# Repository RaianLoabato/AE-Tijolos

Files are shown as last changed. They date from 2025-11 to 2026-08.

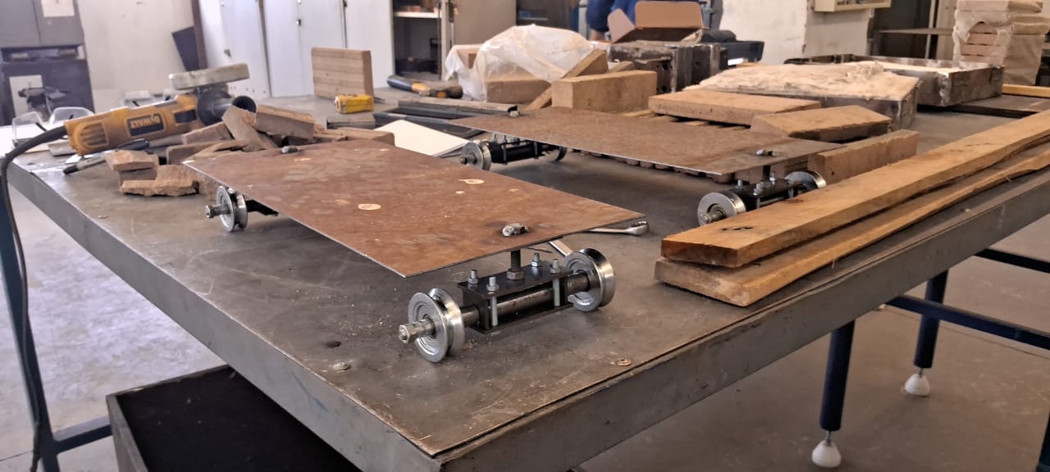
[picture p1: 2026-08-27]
AE-II/AE2 - imagens relatório/nov - 27 de novembro/carrinhos montados.jpeg

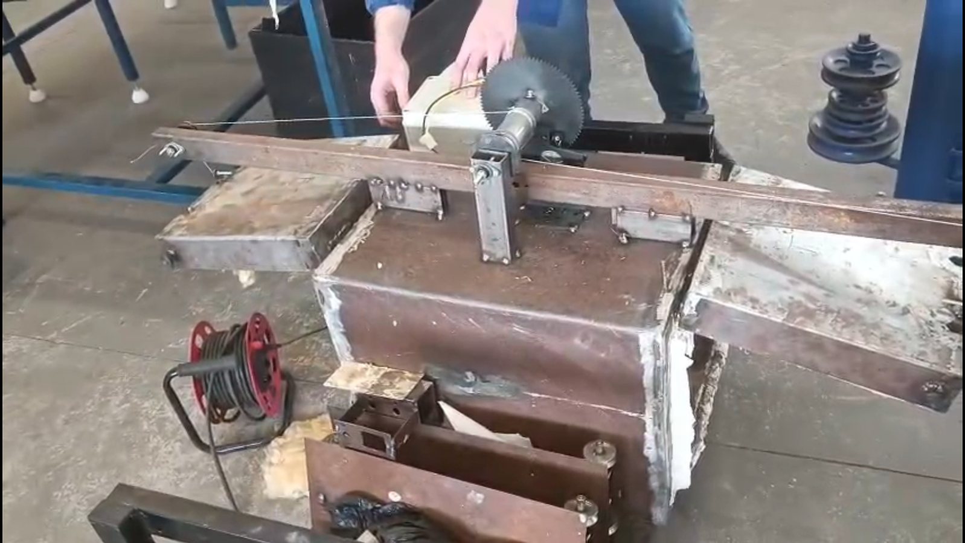
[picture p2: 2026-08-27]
AE-II/AE2 - imagens relatório/dez - 11 de dezembro/teste da elevação das portas refeita 2.png

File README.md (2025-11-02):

O presente trabalho descreve o desenvolvimento de um protótipo de forno automatizado destinado ao controle de temperatura e ao carregamento/descarregamento automático de tijolos. O projeto foi conduzido a partir da identificação de uma demanda real da Olaria Modesto, no Rio Grande do Sul, que necessita modernizar seu processo de fabricação de tijolos diante de uma produção média de 30.000 unidades diárias. Com base em metodologias de projeto integradas, presentes no livro Projeto Integrado de Produtos, o estudo combina conceitos de engenharia, automação e gestão de produto. O referencial teórico contempla a evolução histórica do tijolo, desde construções primitivas até o uso atual como elemento de vedação, e destaca a regulação técnica através de normas como as do INMETRO. A metodologia adotada incluiu análise de requisitos do usuário, projeto conceitual e projeto detalhado. Foram abordadas também tecnologias aplicadas à automação do sistema, como protocolos de comunicação industriais (Modbus, Profibus, Profinet), sensores de deslocamento (LVDT, RVDT, encoder), displays (LCD, OLED), métodos de segurança (chaves criptográficas, reconhecimento facial) e controladores (CLP, ESP 32, Raspberry Pi, etc.). O transporte automatizado dos tijolos é estruturado com sistemas de movimentação por pinhão-cremalheira e corrente. A integração com veículos guiados automaticamente (VGAs) e o uso de motores (com e sem escovas) asseguram a movimentação sincronizada com o ciclo térmico do forno.

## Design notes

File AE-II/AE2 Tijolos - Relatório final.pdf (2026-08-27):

## CURSO SUPERIOR DE ENGENHARIA DE CONTROLE E AUTOMAÇÃO

## TRABALHO DE ATIVIDADE DE EXTENSÃO II

## SISTEMA AUTOMATIZADO DE COZIMENTOS DE TIJOLOS

## EDUARDO PAZ PUTTI

## JOÃO EMILIANO HELRIGHEL FREITAS

## GABRIEL DETTENBORN

## RAIAN LOBATO

Chapecó, SC, Brasil.
6º SEMESTRE – 2025/2

### Sumário

### 1. Introdução 1.1. Demanda do projeto

2. Justificativa do projeto

### 3. Metodologia de pesquisa 3.1. Fundamentação teórica

3.1.1. Termopar tipo K
3.1.2. Transmissor HT-010
3.1.3. Condicionador HW-685
3.1.4. Relé de estado sólido
3.1.5. Ponte H L293n
3.1.6. Motores Mabuchi
3.1.7. Auto transformador variac
3.1.8. Fonte 12V Colmeia
3.1.9. Fonte 5V 2A
3.1.10. ESP 32
4. Modelagem e Equacionamento
4.1. Cálculos da redução de escala
4.2. Cálculos da distância correta entre centros da movimentação do carrinho
4.3. Cálculos do dimensionamento do motor necessário
4.4. Cálculos do dimensionamento da resistência
4.5. Modelagem dos circuitos elétricos
4.5.1. Modelagem do acionamento da resistência
4.5.2. Modelagem do recebimento da temperatura
4.5.3. Modelagem eletromecânica de elevação da porta

### 5. Processos de Fabricação

5.1. Dia 25 de setembro
5.2. Dia 4 de outubro
5.3. Dia 14 de outubro
5.4. Dia 16 de outubro
5.5. Dia 21 de outubro
5.6. Dia 6 de novembro
5.7. Dia 19 de novembro
5.8. Dia 27 de novembro
5.9. Dia 3 de dezembro
5.10. Dia 10 de dezembro
5.11. Dia 11 de dezembro
5.12. Dia 15 de dezembro
5.13. Dia 16 de dezembro
5.14. Dia 17 de dezembro
5.15. Dia 18 de dezembro
6. Resultados
7. Conclusão

### Referências Bibliográficas

### 1. Introdução

A fabricação de tijolos cerâmicos é um processo fundamental para a construção civil, porém ainda é realizada, em muitas olarias, por meio de fornos a carvão com controle térmico limitado. Na Olaria Modesto, assim como em diversas olarias de grande porte, a produção ocorre em grandes bateladas, com os tijolos empilhados em grande quantidade. Essa configuração, unida à ausência de controle de temperatura, resulta em aquecimento não uniforme, ocasionando defeitos, quebras e variações de qualidade dentro de uma mesma produção.
Como consequência, uma parcela significativa das amostras produzidas é descartada ou comercializada com menor valor, gerando perdas econômicas diretas para a empresa. Além disso, o elevado consumo de carvão contribui para o aumento dos custos operacionais e para impactos ambientais.
Embora a utilização de um forno elétrico implique maior consumo de energia elétrica, essa alternativa mostra-se tecnicamente e economicamente viável, uma vez que o controle preciso de temperatura e a maior uniformidade da queima tendem a reduzir drasticamente a taxa de defeitos. Dessa forma, a diminuição das perdas na produção e a melhoria da qualidade dos tijolos permitem que o custo com energia seja compensado pelo aumento da quantidade de peças comercializáveis. Além do retorno financeiro, a padronização e a elevação da qualidade dos produtos aumentam a confiabilidade da empresa no mercado, fortalecendo sua competitividade. Diante disso, este trabalho propõe o desenvolvimento de um forno elétrico automatizado, capaz de atingir temperaturas de até 950°C, com foco no controle térmico, no isolamento adequado e na automação do processo de carga e descarga por meio de portas e carrinhos motorizados.

### 1.1. Demanda do projeto

A demanda analisada neste estudo de caso tem origem na situação da Olaria Modesto, localizada no Rio Grande do Sul, cuja atividade principal consiste na fabricação de tijolos maciços e furados destinados ao setor da construção civil. Com uma produção média diária de 30.000 unidades, necessita a aplicação de soluções tecnológicas que possam aprimorar os processos produtivos e logísticos dados à sua demanda.
A Olaria Modesto, inscrita no CNPJ nº 15.739.566/0001-07 e representada por Alesson Guth Modesto, enfrenta desafios como a necessidade de maior agilidade nas etapas de carregamento e descarregamento assim como na paridade na queima de tijolos.
Considerando que as etapas de inserção e remoção dos tijolos, bem como o monitoramento da temperatura, são atualmente realizadas de forma manual, observa-se a demanda na implantação de sistemas automatizados. Dessa maneira, propõe-se a automatização integral dos processos, englobando desde a entrada dos tijolos até o seu processamento e posterior retirada, com vistas a assegurar ganhos em produtividade, qualidade e segurança.

### 2. Justificativa do projeto

Do ponto de vista científico e tecnológico, o desenvolvimento de um forno elétrico automatizado para a queima de tijolos cerâmicos permite a aplicação prática de conceitos de controle térmico, isolamento térmico, automação e eficiência energética. O projeto possibilita o estudo do comportamento térmico em altas temperaturas, contribuindo para a melhoria e modernização de processos produtivos tradicionais.
Sob a perspectiva social e econômica, a proposta busca solucionar um problema real enfrentado por olarias, como a elevada perda de produção devido à falta de uniformidade na queima. A redução de defeitos nos tijolos diminui o desperdício de material e melhora a rentabilidade da empresa, além de reduzir o consumo excessivo de carvão, contribuindo para a preservação ambiental. A melhoria da qualidade dos produtos também aumenta a confiabilidade da empresa no mercado, impactando positivamente a economia local e a geração de renda.
Em termos pessoais e acadêmicos, o projeto representa uma oportunidade de aplicar, de forma integrada, conhecimentos adquiridos ao longo da formação técnica, envolvendo eletrônica, automação, controle e sistemas térmicos. Além disso, o desenvolvimento de uma solução baseada em uma demanda real fortalece o aprendizado prático, o trabalho em equipe e a capacidade de propor soluções viáveis para problemas da sociedade.

### 3. Metodologia de pesquisa

Este trabalho utiliza uma metodologia de caráter prático e aplicado, com o objetivo de desenvolver um protótipo de forno automatizado para controle de temperatura e para o carregamento e descarregamento automático de tijolos.
O livro Projeto Integrado de Produtos foi utilizado como base para orientar o desenvolvimento do projeto. A metodologia apresentada no livro auxiliou na organização das etapas, desde o planejamento inicial até a construção e avaliação do protótipo, permitindo uma visão integrada do produto.
As etapas de metodologia consistem em projeto informacional, projeto conceitual, projeto preliminar e projeto detalhado, é possível acessar as etapas do projeto informacional até o início do projeto preliminar em [1].

### 3.1. Fundamentação teórica

A produção de materiais cerâmicos exige um controle térmico, pois a qualidade final do produto depende diretamente da estabilidade e da uniformidade da temperatura durante o processo de queima. Temperaturas mal distribuídas podem causar defeitos estruturais, trincas e variações nas propriedades mecânicas dos tijolos [2].
Sistemas de medição de temperatura em altas faixas térmicas são amplamente utilizados na indústria, sendo os sensores termoelétricos uma solução eficiente devido à sua robustez e confiabilidade. A correta leitura desses sensores depende do condicionamento e da conversão adequada dos sinais, garantindo precisão e segurança no controle do processo.
Além disso, sistemas de acionamento eletromecânico, como motores controlados eletronicamente, são necessários para automatizar movimentos de portas e transporte de materiais, reduzindo a intervenção humana e aumentando a segurança operacional [2].
Dessa forma, a integração entre sensoriamento, controle automático e acionamento eletromecânico constitui a base teórica para o desenvolvimento de fornos industriais modernos e eficientes, como o proposto neste trabalho [2].
3.1.1. Termopar tipo K

A termorresistência termoelétrica (termopar) explora o efeito Seebeck: quando duas ligas metálicas diferentes formam uma junção e há diferença de temperatura entre a junção de medição e a junção de referência, surge uma força eletromotriz (EMF) aproximadamente proporcional à diferença térmica. O termopar tipo K, constituído por uma liga Ni-Cr (positivo) e Ni-Al (negativo), é um dos tipos mais usados por oferecer ampla faixa de medição (tipicamente −200 °C a ~1 260 °C em aplicações industriais) e boa resistência mecânica e químico-térmica em atmosferas oxidantes. Para fundamentos do efeito termoelétrico e integração de sensores como elemento de um sistema de medição recomenda-se consultar livros de instrumentação e sistemas de medição que tratam da teoria do Seebeck, acoplamento térmico e condicionamento de sinais [3].

Fig 1 . Termopar tipo K

Fonte: [4]

As características elétricas e a precisão prática dos termopares tipo K são definidas por funções de referência e tabelas calibradas (EMF versus temperatura) baseadas na Escala

Internacional de Temperatura ITS-90; essas relações são formalizadas em normas técnicas (por exemplo, IEC 60584-1 e a especificação ASTM E230), que definem também as classes de tolerância e limites de aplicação. Para medições rigorosas é comum usar as polinomiais ou tabelas ITS-90/NIST como padrão de referência e aplicar as tolerâncias especificadas pelas normas ao escolher pares de fios e cabeamento de extensão. A literatura técnica e monografias NIST fornecem as tabelas de referência e as expressões para conversão EMF por temperatura utilizadas em calibração e software de aquisição [5].
Na prática, a acurácia final depende de fatores além da curva característica: qualidade e homogeneidade do fio termopar, soldagem/terminação da junção, deriva (derretimentos ou contaminação das ligas em altas temperaturas), e a compensação correta da junção fria (cold-junction compensation). Notas de aplicação de fabricantes e integradores (por exemplo, guias da indústria e notas técnicas de fabricantes de condicionadores e ADCs) detalham erros típicos, métodos de calibração, e boas práticas de instalação (blindagem, aterramento, proteção mecânica e seleção de isolantes compatíveis). Para projeto de aquisição de dados, é recomendado seguir tanto as normas (IEC/ASTM) quanto os guias de fabricantes para escolher classe de termopar, técnicas de compensação e procedimentos de calibração periódica [6].
3.1.2. Transmissor HT-010

O transmissor de temperatura HT-010 é um conversor de sinais projetado para interfaces industriais, que recebe o sinal de sensores de temperatura — como termopares e sensores de resistência (RTD) — e o condiciona para uma saída padronizada de corrente na faixa de 4-20 mA, compatível com sistemas de aquisição e controle (PLC, DCS, instrumentos) [7]. O HT-010 é configurável via interface USB e pode aceitar entradas de vários tipos de termopar (inclusive tipo K) ou sensores RTD, e internamente aplica compensação de junção fria (cold junction compensation), essencial para medições com termopares devido à natureza diferencial do sinal térmico (pequenos milivolts) gerado pelo par metálico.
Quando um termopar tipo K é conectado ao HT-010, o dispositivo monitora a tensão termoelétrica gerada pela junção quente do termopar. Essa tensão é proporcional à diferença de temperatura entre a junção quente e a referência (junção fria) no transmissor. Como as tensões geradas por termopares são muito pequenas (em milivolts) e suscetíveis a ruídos e deriva térmica, o HT-010 inclui um estágio de condicionamento de sinal que amplifica, filtra e lineariza essa tensão de entrada com base nas curvas de resposta específicas do tipo K. Além disso, a compensação de junção fria interna ajusta o sinal para uma referência de temperatura conhecida, necessária para a precisão da medição [8]. O HT-010 incorpora compensação interna de junção fria, recurso fundamental para eliminar erros associados à temperatura do ponto de referência do termopar. A precisão especificada de 0,5% para entradas TC, aliada à baixa deriva térmica (25 ppm/°C em fundo de escala), indica que o condicionamento interno — composto por amplificação, filtragem e linearização conforme o tipo de termopar selecionado via software [8].

Fig 2 . Transmissor HT-010

Fonte: Autoria Própria (2025)

A carga (resistência) conectada ao transmissor, tipicamente um resistor ou o terminal de entrada de um controlador, deve estar dentro da capacidade de carga permitida pelo laço (por exemplo, até algumas centenas de ohms dependendo da tensão de alimentação e especificação do transmissor) para garantir que a corrente seja mantida corretamente pelo laço [8].
A carga na figura abaixo é representada pelo receptor do sinal de 4 a 20mA, cuja capacidade de carga especificada (250 Ω ou até 500 Ω, dependendo da tensão de alimentação entre 12 e 35 VDC) garante que a corrente seja mantida dentro dos limites mesmo em instalações com cabos longos ou entradas de alta impedância [8].

Fig 3 . Diagrama de ligação transmissor com termopar

Fonte: [9]

3.1.3. Condicionador HW-685

O HW-685 é um módulo condicionador de sinal destinado a converter sinais industriais de corrente (0–20 mA / 4–20 mA) em uma tensão proporcional (0–3,3 V, 0–5 V ou 0–10 V), permitindo a leitura por microcontroladores e ADCs comuns. Funcionalmente trata-se de um "shunt ativo" com ajustes de ganho e offset (potenciômetros de ZERO e SPAN), e normalmente incorpora proteção contra inversão de polaridade e indicação por LED de alimentação [10].
A tensão de alimentação é tipicamente entre 7–30 V (algumas versões 12–35 V), com uma faixa de entrada de 0–20 mA ou 4–20 mA. A saída do sinal é configurável para 0–3,3 V, 0–5 V, 0–10 V [11].
O condicionador possui uma deriva térmica na ordem de ±100 ppm/°C e dimensões compactas (~40 × 25 × 12 mm). Também possuem indicações de faixas de operação ambiental entre −10 °C a 60 °C e capacidade de operação em laços com até algumas centenas de ohms de carga, conforme a versão do módulo [12].

Fig 4 . Condicionador HW-685

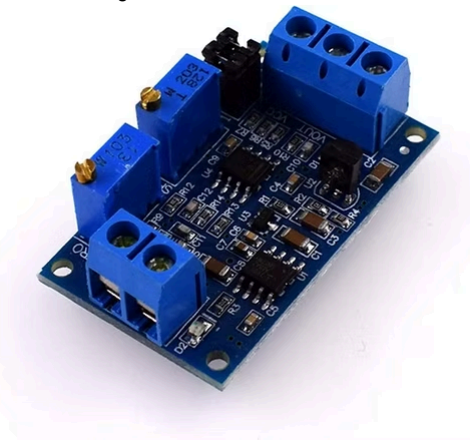
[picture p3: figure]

Fonte: [10]

As conexões típicas do HW-685 refletem sua função final: o sinal de corrente entra pelo terminal de entrada (sendo possível conectar o laço 4-20 mA vindo de um sensor/transmissor), que pode realizar o papel de carga para o transmissor, como o HT-010. O módulo converte esse fluxo de corrente em uma queda de tensão controlada e ajustável, e disponibiliza essa tensão no pino de saída para leitura por ADC. Ajustes de ZERO e SPAN permitem calibrar o ponto de 4 mA (ou 0 mA) e 20 mA para corresponder às tensões mínimas e máximas desejadas.
O módulo possui dois jumpers que são usados para configurar o sinal de referência para o VCC, que corresponderá ao valor máximo da saída no Vout. Além disso, é possível regular os dois potenciômetros para calibrar a tensão mínima(0V) e a tensão máxima, o diagrama representativo é visto na figura abaixo.

Fig 5 . Configurações gerais do HW-685

Fonte: [13]

3.1.4. Relé de estado sólido

O relé de estado sólido SSR-40DA é um dispositivo eletrônico de comutação projetado para controlar cargas de corrente alternada (AC) a partir de um sinal de controle em corrente contínua (DC), sem o uso de partes móveis como nos relés eletromecânicos. Em vez de contatos físicos, ele utiliza componentes semicondutores — tipicamente triacs ou pares de SCRs em configuração antiparalela — que permitem a abertura e fechamento do circuito de saída com maior rapidez, silêncio operacional e maior vida útil devido à ausência de desgaste mecânico. Essa estrutura também oferece isolamento entre os circuitos de controle e de potência, reduzindo interferências e aumentando a segurança elétrica no comutador de cargas industriais e automação [14].
O SSR-40DA opera com uma tensão de controle de 3 a 32 VDC na entrada, adequada para ser acionada por microcontroladores, módulos lógicos ou mesmo transmissores industriais que entregam sinais DC nesse intervalo. A saída está projetada para controlar cargas em AC com faixa de 24 a 380 VAC e suportar correntes de até 40 A de forma contínua, o que o torna apto a ligar e desligar aquecedores, motores monofásicos e outros dispositivos de potência em aplicações industriais e de processo [15]. O tempo de resposta típico é de aproximadamente 10 ms para ligar ou desligar, e o relé usa um método de disparo por passagem por zero (zero cross trigger), que reduz ruído elétrico e picos de corrente ao sincronizar a comutação com o cruzamento do sinal AC por zero volt. A queda de tensão em estado ligado é baixa (~1,5 V), e a corrente de fuga no estado desligado é pequena, normalmente alguns miliamperes, embora não nula, o que é importante considerar em alguns projetos [15].

Fig 6 . Relé de estado sólido

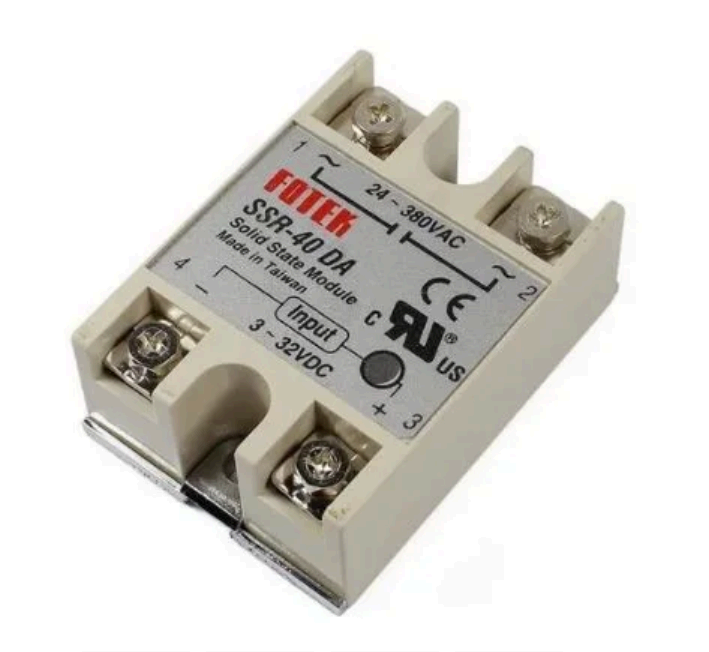
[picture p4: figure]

Fonte: [14]

3.1.5. Ponte H L293n

O L293 (e suas variantes como L293N / L293D) é um circuito integrado do tipo quadruple half-H driver — essencialmente quatro drivers push-pull integrados que podem ser usados em pares para formar duas pontes H independentes. Projetado para acionar cargas indutivas (motores DC, solenoides, relés, motores de passo bipolares), o dispositivo aceita sinais lógicos TTL/CMOS no lado de entrada e fornece correntes de saída relativamente altas sobre uma faixa de tensões de alimentação para os motores (tipicamente 4,5 V a 36 V) [16]. Cada saída é um estágio transistorizado capaz de conduzir corrente contínua e picos não repetitivos mais altos por curtos instantes; variantes como a L293D incluem diodos de proteção internos para supressão de transientes indutivos [16].

A alimentação é dividida em dois domínios: uma fonte para a lógica de controle (Vcc1), tipicamente de 5 V, e uma fonte separada para a carga (Vcc2), que pode variar aproximadamente de 4,5 V até 36 V. Cada canal de saída suporta correntes contínuas da ordem de centenas de miliampères a até 2 A, com capacidade de picos maiores por curtos intervalos, característica relevante para vencer a inércia inicial de motores [16].

Fig 7 . Ponte H L293n

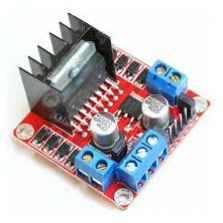
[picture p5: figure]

Fonte: [17]

Os pinos de entrada lógica (IN1, IN2, IN3 e IN4) determinam o estado de condução de cada meio-ponte e, consequentemente, o sentido da corrente aplicada à carga. Associados a estes pinos estão os pinos de habilitação (Enable), que permitem ativar ou desativar cada par de saídas e são amplamente utilizados para aplicação de sinais PWM de forma errada, pois deve apenas indicar o acionamento e deixar o PWM para ser executado nas entradas lógicas para prolongar vida útil da ponte H.
Os pinos de saída (OUT1 a OUT4) conectam-se diretamente às cargas, conduzindo a tensão proveniente da alimentação de potência (Vcc2) conforme a combinação lógica aplicada às entradas. A presença de pinos de alimentação separados para lógica e potência, bem como múltiplos pinos de terra distribuídos no encapsulamento, reflete a preocupação do projeto em reduzir interferências e garantir estabilidade elétrica. Em variantes como a L293D, a ficha técnica ainda indica a incorporação de diodos de proteção internos, associados à pinagem de saída, para suprimir sobretensões geradas por cargas indutivas, simplificando o projeto e aumentando a robustez do sistema [16].

Fig 8 . Ponte H L293n detalhada

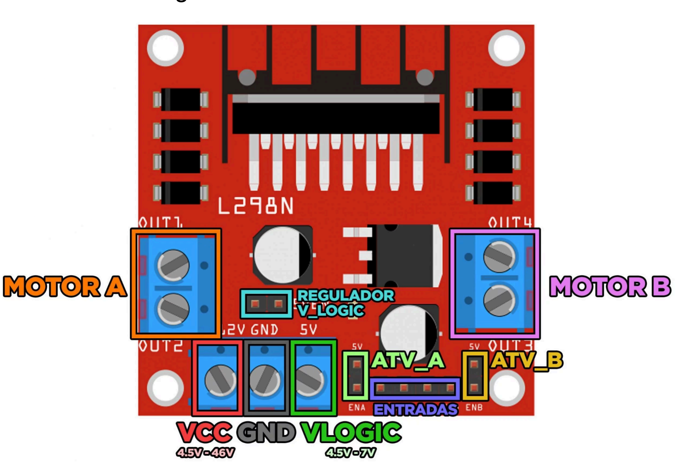
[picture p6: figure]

Fonte: [18]

3.1.6. Motores Mabuchi

Os motores Mabuchi são motores de corrente contínua de 12 VDC com escovas, projetado para fornecer alto torque em baixas rotações e elevada robustez mecânica. Esses motores são desenvolvidos para operar em ambientes severos, sujeitos a vibração, variações térmicas e umidade, características típicas da aplicação automotiva. Do ponto de vista construtivo, o motor emprega ímãs permanentes no estator e um rotor bobinado com comutador, permitindo conversão direta de energia elétrica em energia mecânica por meio da interação eletromagnética. A escolha de 12 VDC como tensão nominal decorre da padronização do sistema elétrico veicular, garantindo compatibilidade direta com baterias automotivas e sistemas de controle embarcados.

Fig 9 . Motor Mabuchi visão frontal

Fonte: [19]
O motor Mabuchi de 12 VDC apresenta, em sua forma mais simples, dois terminais principais para alimentação, sendo o sentido de rotação definido pela polaridade aplicada. Em versões automotivas específicas, como as destinadas a limpadores de para-brisa, é comum a presença de terminais adicionais associados a contatos de posição ou sistemas internos de comutação, responsáveis por garantir o retorno automático das palhetas à posição de repouso. Esses contatos permitem que o motor continue girando até atingir um ponto angular específico, mesmo após o desligamento do comando principal, funcionalidade crítica para o correto funcionamento do sistema de limpeza do para-brisa.

Fig 10 . Motor Mabuchi visão traseira

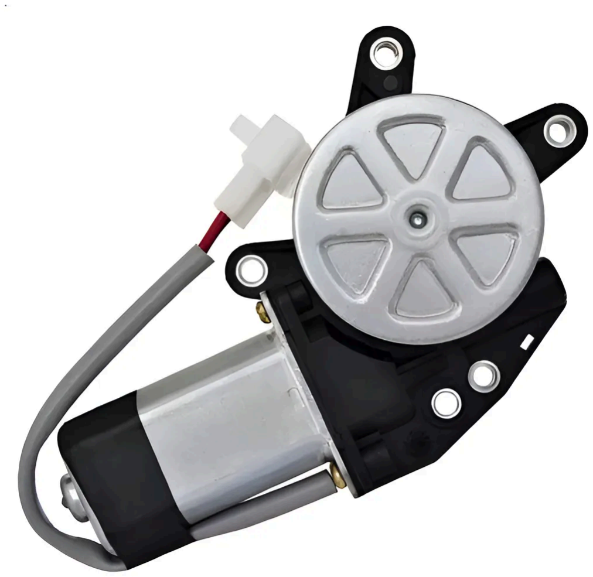
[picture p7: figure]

Fonte: [19]

3.1.7. Auto transformador variac

O autotransformador variável, popularmente conhecido como Variac (marca originalmente associada à General Radio), é um dispositivo eletromagnético utilizado para fornecer tensão AC ajustável de forma contínua, mantendo a mesma frequência da rede elétrica. Diferentemente do transformador convencional, o Variac utiliza um único enrolamento com deriva móvel, permitindo que a tensão de saída seja obtida como uma fração (ou ligeiramente acima, em alguns modelos) da tensão de entrada. Essa característica reduz perdas por cobre e tamanho físico quando comparado a transformadores isoladores de mesma potência, porém elimina o isolamento galvânico entre entrada e saída — aspecto amplamente discutido na literatura de máquinas elétricas [20]. O Variac pode ser considerado como um caso particular de autotransformador, enfatizando sua operação baseada na indução eletromagnética e na proporcionalidade entre número de espiras e tensão induzida (V ∝ N), conforme a lei de Faraday [20].

Fig 11 . Auto Transformador variável

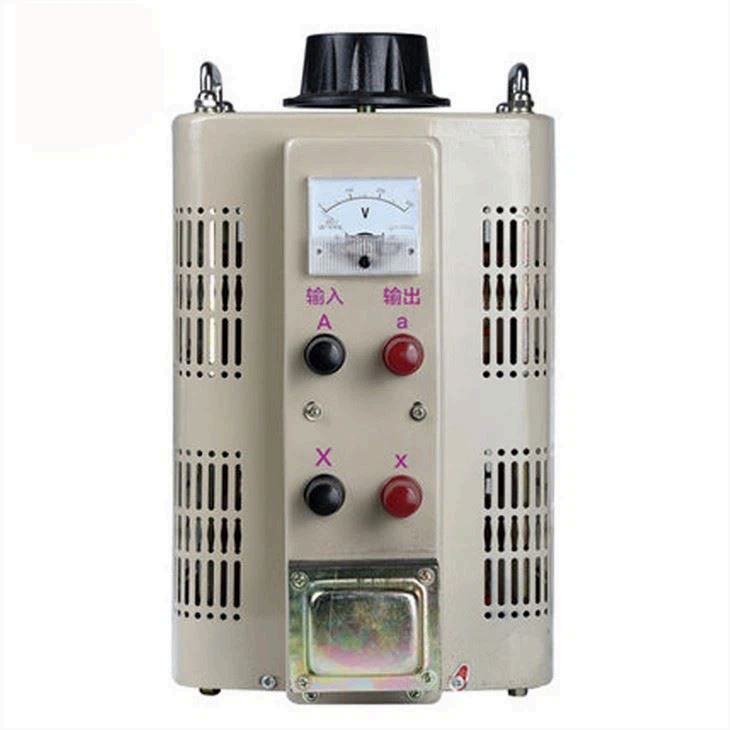
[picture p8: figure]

Fonte: [21]

3.1.8. Fonte 12V Colmeia

A fonte de alimentação de 12 V do tipo colmeia é responsável por fornecer energia elétrica aos dispositivos que operam nessa tensão, como motores e módulos de acionamento. Esse tipo de fonte é utilizada em sistemas de automação por apresentar boa capacidade de corrente, ao entregar 20A, ventilação adequada e proteção contra sobrecarga, que garante o funcionamento estável e seguro do sistema.

Fig 12 . Fonte 12v colmeia

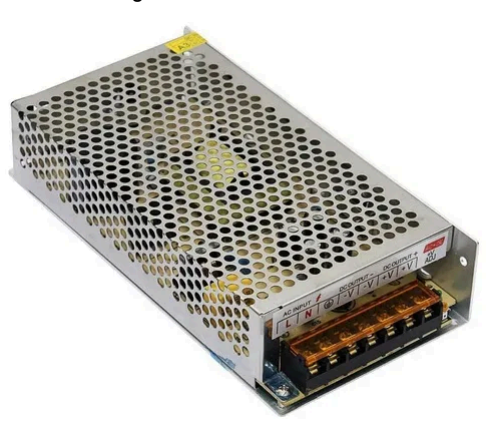
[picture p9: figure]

Fonte: [22]

3.1.9. Fonte 5V 2A

A fonte de alimentação de 5 V com corrente nominal de 2 A é utilizada para alimentar os circuitos de controle e dispositivos eletrônicos de baixa potência, como por exemplo um microcontrolador ESP32 e módulos de sinal.

Fig 13 . Fonte 5v

Fonte: [23]

3.1.10. ESP 32

O ESP32 atua como a unidade central de controle do sistema. Esse microcontrolador é responsável por realizar a leitura dos sensores, processar as informações e comandar os atuadores, como relés e motores. Sua elevada capacidade de processamento, aliada à grande quantidade de portas de entrada e saída, torna-o adequado para aplicações de automação e controle industrial.

Fig 14 . ESP 32

Fonte: [24]

### 4. Modelagem e Equacionamento

### 4.1. Cálculos da redução de escala

O primeiro passo foi a realização do cálculo da redução do forno com base na proporção do volume suportados pelos carrinhos e a dimensão real do forno, sendo: o C o prefixo que indica

comprimento; L o prefixo que indica largura ; A a altura ; P o peso; V o volume e Q a quantidade.

C

tijolo = 140 mm

L

tijolo = 90 mm

A

tijolo = 190 mm

P

tijolo = 3 kg

Qtijolo = 30000

V | (1)
tijolo = C
tijolo

× L
tijolo

× A

tijolo = 0, 0024 m

3

V | (2)
total = Qtijolo

× V

| tijolo = 71, 82 m

P

total = Qtijolo

× P

| tijolo = 90000 kg

C

carrinℎo = 250 mm

L

carrinℎo = 260 mm

A

carrinℎo = 251 mm

V

carrinℎo = C
carrinℎo

× L
carrinℎo

× A

| carrinℎo = 0, 0163 m

3
(3)
α = | (4)

V
total
2 × V
carrinℎo

= 2201

Com a redução de 2201 vezes encontrada, foi diagnosticada uma necessidade da redução do tamanho do tijolo, para evitar ter de trabalhar com 30000 tijolos com escalas micrométricas. Para isso foi decidido arbitrariamente o coeficiente de 2 vezes, para assegurar tijolos com dimensões realistas para processos de fabricação. Com o fator de 2 vezes foi possível calcular a quantidade de tijolos a serem fabricados no projeto:

α

tamanℎo = 2

C | (5)
tijolo−r = C
tijolo

× α
tamanℎo
| −1 = 0, 07 m
L | (6)
tijolo−r = L
tijolo

× α
tamanℎo
| −1 = 0, 045 m
A | (7)
tijolo−r = A
tijolo

× α
tamanℎo
| −1 = 0, 095 m
Q | (8)
tijolo−r−c =

C
carrinℎo
C
tijolo−r
| = 3, 5714
Q | (9)
tijolo−r−l =

L
carrinℎo
L
tijolo−r

= 5, 7778

Q | (10)
tijolo−r−a =

A
carrinℎo
A
tijolo−r

= 2, 6421

Q | (11)
tijolos−carrinℎo = 3 × 5 × 2 = 30
Q | (12)
tijolos−forno = 2 × Qtijolos−carrinℎo = 60

### 4.2. Cálculos da distância correta entre centros da movimentação do carrinho

Para o cálculo da distância entre centros usada para os eixos de movimentação do carrinho visto em [1], é necessário antes definir algumas constantes, como o número de dentes, o passo da polia e a distância entre centros aproximados. Com isso é possível encontrar o número de elos para corrente e em seguida a distância correta entre centros, visto em [25]:

Z = 15

T = 12, 7 × 10

m

Qaproximado = 0, 2 m

Y | (13)
elos−aproximado = Z + 2 ×

C
aproximado
T = 46, 4961

Y

elos = 46

C | (14)
r =

T
4 × (Y

elos − Z + (Y

elos − Z)

2
) = 0, 197 m

### 4.3. Cálculos do dimensionamento do motor necessário

Para o cálculo do dimensionamento do motor usado para elevação da porta, é necessário calcular o torque e a potência nominal mínima exigida pelo motor. Com o peso da porta estimado pelo desenho do Solidworks em [1], e o raio aproximado para a polia do motor é possível realizar os cálculos com fórmulas encontradas em [26]:

M

porta = 3, 5 kg

gravidade = 9. 81 ×

m
s

2

F | (15) mínima = M
porta

× gravidade = 34, 335 N

V

ideal = 0, 2

m
s
P | (16) mínima = F
mínima

× V

ideal = 6, 867 W

ηmotor = 0. 60 kg

P | (17) mínima−motor =

P
mínima
ηmotor

= 11, 445 W

r

polia = 0. 0208 m

T | (18) mínimo = F
mínima

× r
polia
T

mínimo ≈ 0, 7142 N × m

Com esses valores conseguimos encontrar um motor ideal para o nosso projeto, o motor Mabuchi de 12V:

V

motor = 12

Imotor = 7, 5 A

P | (19) motor = V
motor

× Imotor = 90 W

P

motor > P

mínima−motor = 1

T | (20) motor = 3 N × m

T

motor > T

mínimo = 1

### 4.4. Cálculos do dimensionamento da resistência

Partindo de uma resistência de 10 metros de NiCr com 1mm de diâmetro:

ρ

NiCr = 1, 10 × 10

−6Ω × m , a 20 °C

r = | (21)

d
2 = 0. 0005 m

A = 7, 85398 × 10

| −7 m
| 2
R = ρ × | (23)

L
A
R ≈ 14, 0056 Ω
I = | (24)

V
R =

220
14,0056 = 15, 708 A
P = | (25)

V

2
R =

220

2
14,0056 = 3455, 761 W
V | (26)
pp = 220 × 2 = 311 V
I | (27)
pp = 16 × 2 = 23 A

Triac => (+ 23A e + 311V)

Para simplificar o processo de chaveamento, foi utilizado o SSR-40 DA, que consegue entregar os 23A a 311V de pico, e ainda fazer o cruzamento por zero, necessário para evitar um sobreaquecimento no processo de chaveamento durante o controle.

### 4.5. Modelagem dos circuitos elétricos

Para o forno, são utilizadas 4 alimentações, uma de 220VAC para a resistência, uma de 24VDC para acionamento de contatora seguindo a NR12, uma linha de 12VDC para alimentação dos motores, ponte H L293n e o transmissor. E por fim, a alimentação de 5VDC para alimentar o ESP32 e o condicionador HW-685.

4.5.1. Modelagem do acionamento da resistência

Para acionar a resistência seguindo a NR 12, foi realizado o acionamento pelo botão S1, que pode ser desligado pelo S2, ao ligar é possível usar o botão de emergência S0 para desligar e bloquear o sistema, como visto abaixo:
Fig 15 . Circuito de comando

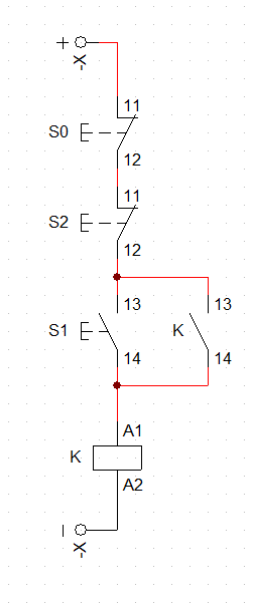
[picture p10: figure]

Fonte: Autoria própria (2025)

A bobina K aciona a contatora K, que é usada para manter o selo no botão de ligar S1 e quando desligada rompe a conexão da resistência.
Antes da corrente da fase chegar na contatora ela passe pelo disjuntor geral F, e depois de passar pelo contator é chaveada pelo relé de estado sólido, que não é representado na figura abaixo, e em seguida segue para a resistência.
Fig 16 . Circuito de força

Fonte: Autoria própria (2025)

Para o posterior controle da resistência, foi utilizado o relé de estado sólido SSR-40 DA, cujos terminais de alta potência são ligados depois da contatora na fase, e os terminais de baixa potência direto no ESP 32 nos pinos 26 e GND.

4.5.2. Modelagem do recebimento da temperatura

O sinal de temperatura é gerado pelo termopar tipo K, convertida em um sinal de 4-20mA pelo transmissor HT-010, condicionada pelo HW-685 para um valor entre 0 e 3,3V e ligado em uma entrada analógica do ESP 32, seguindo os esquemas de ligação da revisão bibliográfica.
Para encontrar a temperatura é usado o princípio de linearidade do sinal condicionado, relacionando os 3,3V com a temperatura máxima de 1200°C e os 0V com a temperatura de 0°C.
T | (28)
lida =

pADC

2

Nbits−1

* 1200°C

Cujo pADC representa a leitura analógica feita pelo ADC, N os números de bits de
bits
resolução do ADC.
4.5.3. Modelagem eletromecânica de elevação da porta

Com a modelagem do motor concluída, foi possível desenvolver sua parte eletrônica. O motor opera em 12V, com picos de até 2A, demanda suprida pela ponte H L293N, utilizada para chaveamento. O PWM é controlado pelo ESP 32, que fornece os sinais de comando, enquanto a alimentação vem da fonte de 12V colmeia e a saída é direcionada ao motor.

### 5. Processos de Fabricação

Durante o processo de fabricação, cada dia foi organizado e estruturado pelo Click Up, para que todos que vieram no dia tenham tarefas, abaixo é registrado as principais modificações feitas.

### 5.1. Dia 25 de setembro

A caixa do forno e o conjunto da porta foram cortadas e soldadas e um acabamento com os discos flap foi executado em ambas as peças, as portas acabadas foram preenchidas com fibra cerâmica. Além disso, foram cortadas chapas para as caixas de movimentação do forno.

Fig 17 . Caixa do forno soldada

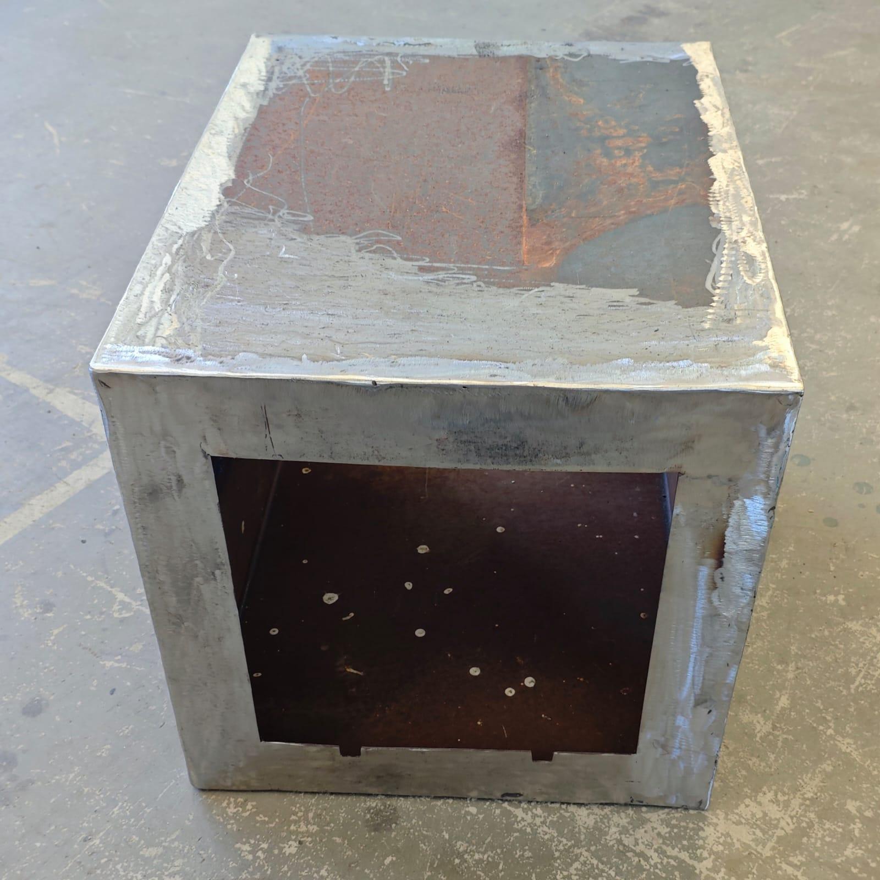
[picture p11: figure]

Fonte: Autoria própria (2025) Fig 18 . Chapas para confecção das caixas de movimentação do motor

Fonte: Autoria própria (2025)

Fig 19 . Inserindo isolação na porta

Fonte: Autoria própria (2025)

Fig 20 . Portas isoladas

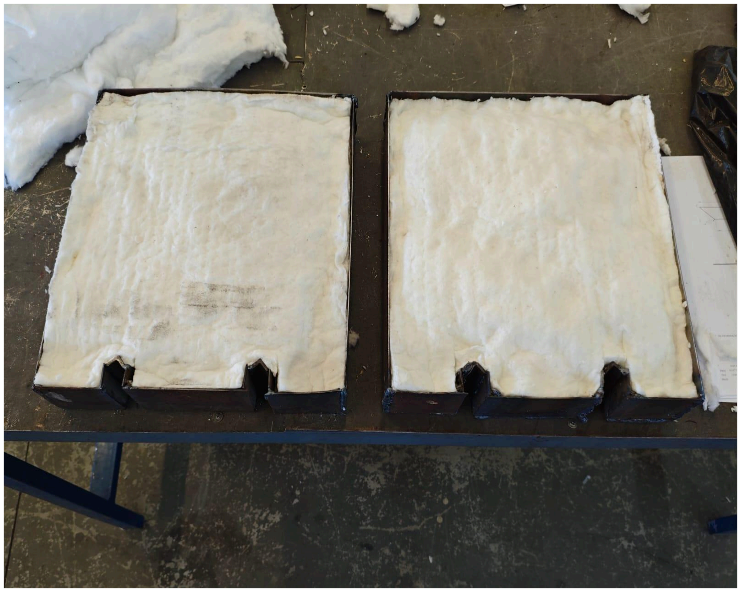
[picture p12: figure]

Fonte: Autoria própria (2025)

### 5.2. Dia 4 de outubro

As chapas das caixas de movimentação do carrinho foram furadas a fim de possibilitar a fixação de mancais as mesmas quando soldadas em sua montagem final.

Fig 21 . Processo de perfuração das chapas das caixas de movimentação

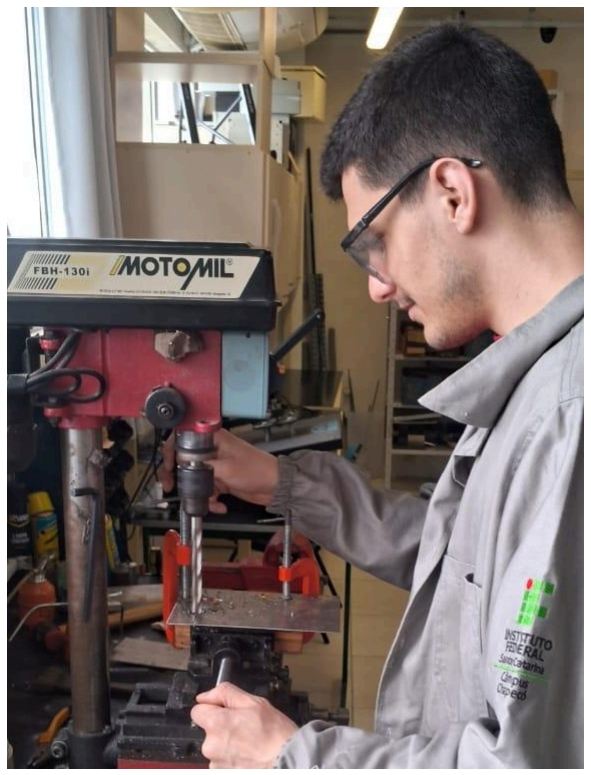
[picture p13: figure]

Fonte: Autoria própria (2025)

### 5.3. Dia 14 de outubro

Enquanto as caixas de movimentação eram fabricadas as peças com função de ser suportes dos motores Mabuchi eram cortadas dobradas e furadas, devido a tolerâncias impróprias dois suportes confeccionados neste dia foram descartados e substituídos por suportes sobressalentes encontrados no ifsc em uma data posterior.

Fig 22 . Suporte de motor com tolerâncias não admissíveis

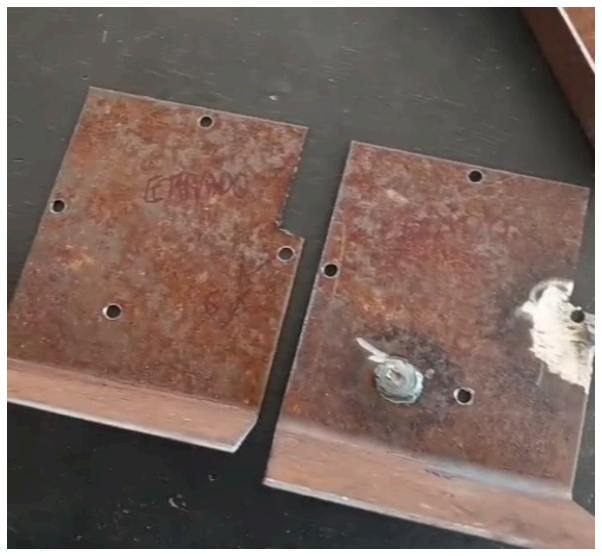
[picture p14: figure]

Fonte: Autoria própria (2025)

### 5.4. Dia 16 de outubro

Após realizar um posicionamento preliminar a fim realizar a fixação com solda dos componentes da elevação vertical da porta, foi constatado que não seria possível manter a plena isolação térmica da máquina com esse modo de elevação devido às grandes frestas necessárias para o funcionamento deste sistema, além disso a trajetória da porta impossibilitaria qualquer adição de material isolante para remediar o empecilho. Assim as peças foram descartadas e um novo sistema de elevação com a porta pivotante para cima foi desenvolvido e construído nos dias seguintes.
Fig 23 . Componentes da elevação da porta

Fonte: Autoria própria (2025) Fig 24 . Avaliando a elevação da porta

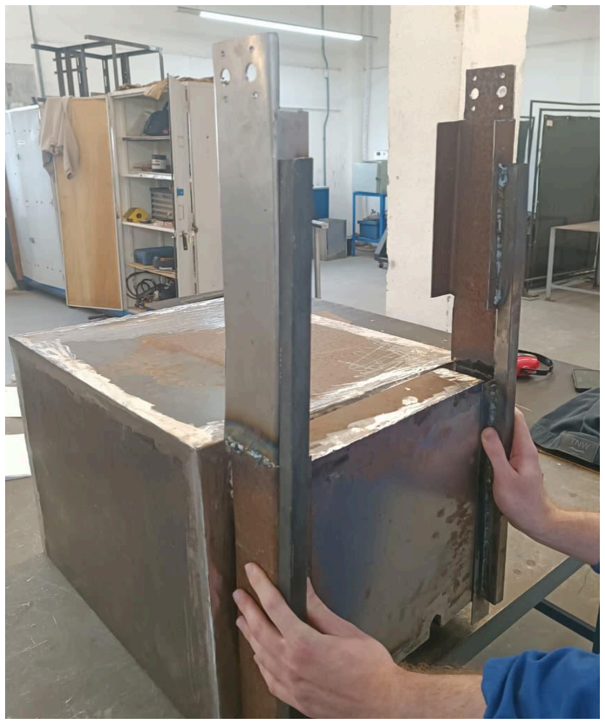
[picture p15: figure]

Fonte: Autoria própria (2025)

### 5.5. Dia 21 de outubro

O forno teve novos cortes realizados nos orifícios para a entrada dos carrinhos para melhor aderir as tolerâncias necessárias para acomodar os trilhos, pois os cortes realizados anteriormente eram muito pequenos.
A confecção do suporte lateral do forno continuou.
O painel elétrico saiu da fase de projetos e iniciou a produção começando com o corte e posicionamento das canaletas utilizadas para acomodar a fiação interna.

Fig 25 . Ajuste nos furos de passagem dos trilhos

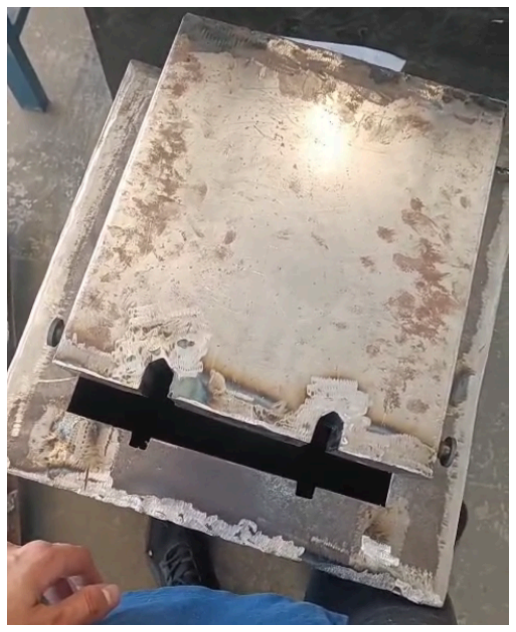
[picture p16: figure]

Fonte: Autoria própria (2025) Fig 26 . Chapas suporte lateral

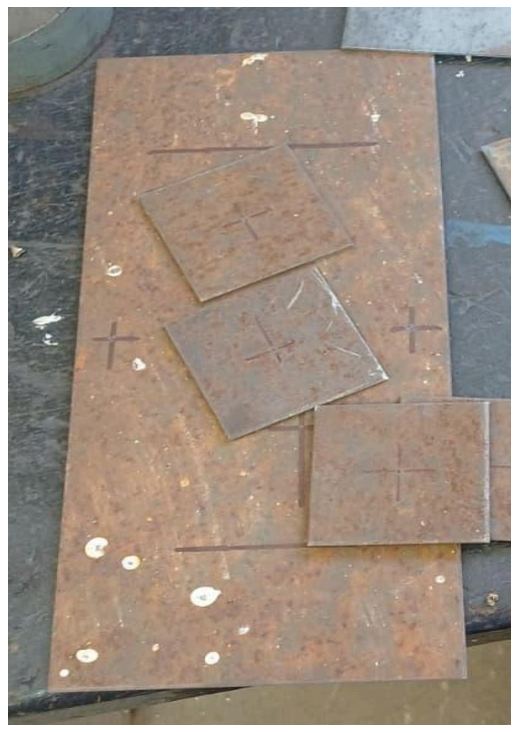
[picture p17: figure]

Fonte: Autoria própria (2025) Fig 27 . Painel elétrico com canaletas

Fonte: Autoria própria (2025)

### 5.6. Dia 6 de novembro

Dobradiças para as portas foram compradas e soldadas a fim de realizar a pivotação vertical para a abertura da porta, uma vez que a elevação da porta por guilhotina se demonstrou inviável. Além disso, foi remodelado o CAD para que seja feito a pivotação nele.
Os rodízios de rodas dos carrinhos foram testados para verificar se o encaixe dos eixos feitos anteriormente estava adequado. Devido a uma bucha que vinha montada nas rodas os eixos tiveram que ser novamente processados no torno mecânico a fim de atingir o diâmetro necessário para o encaixe.
Foi realizada a modificação estrutural de elevação da porta, que ao invés de ter movimentação como uma porta guilhotina, será pivotada, como visto nas figuras abaixo.

Fig 28 . Esboço do projeto em 3D antigo

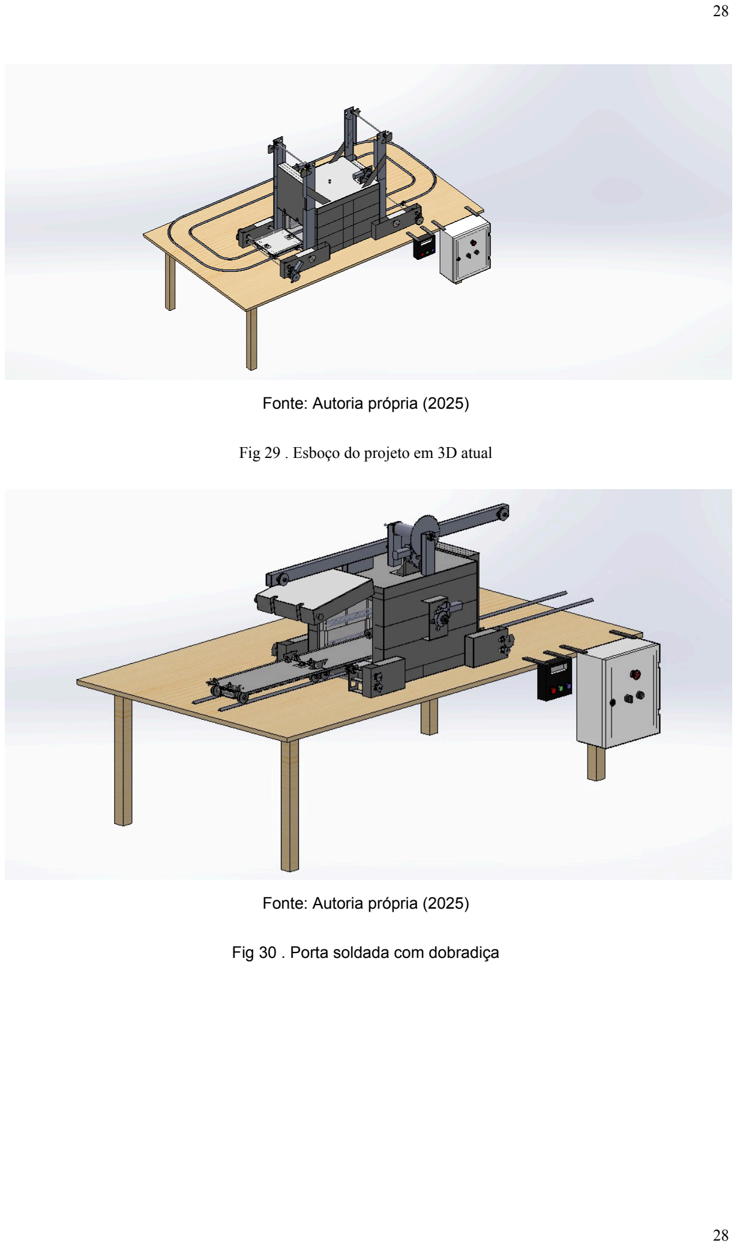
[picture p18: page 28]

Fonte: Autoria própria (2025)

Fig 29 . Esboço do projeto em 3D atual

Fonte: Autoria própria (2025)

Fig 30 . Porta soldada com dobradiça

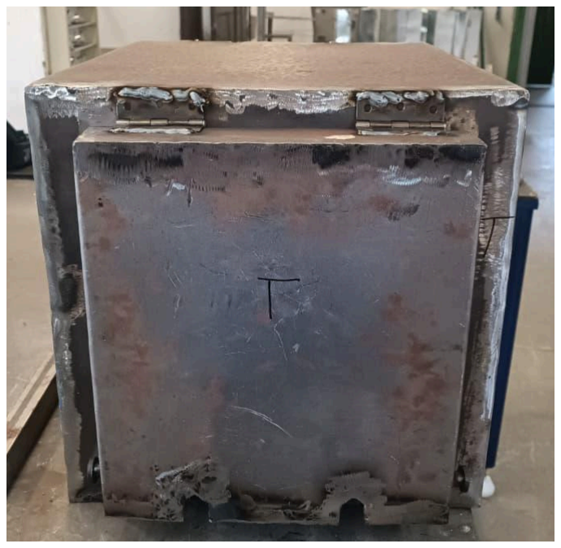
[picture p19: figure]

Fonte: Autoria própria (2025)

Fig 31 . Eixos após o ajuste

Fonte: Autoria própria (2025)

### 5.7. Dia 19 de novembro

Os tijolos comprados pela internet foram retirados do IFSC de Jaraguá do Sul Fig 32 . Tijolos sendo buscados

Fonte: Autoria própria (2025)

### 5.8. Dia 27 de novembro

As paredes e o chão do forno foram cobertos com tijolos refratários para isolamento térmico e os carrinhos foram montados parcialmente.
Fig 33 . Tijolos assentados

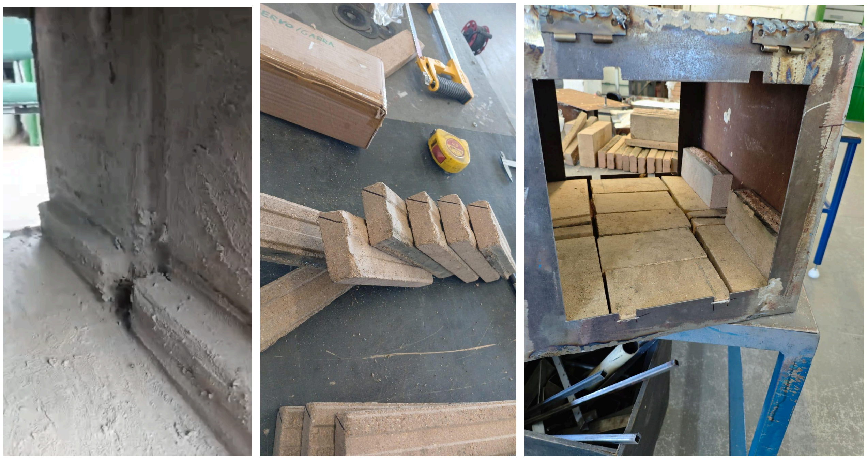
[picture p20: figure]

Fonte: Autoria própria (2025) Fig 34 . Carrinhos montados

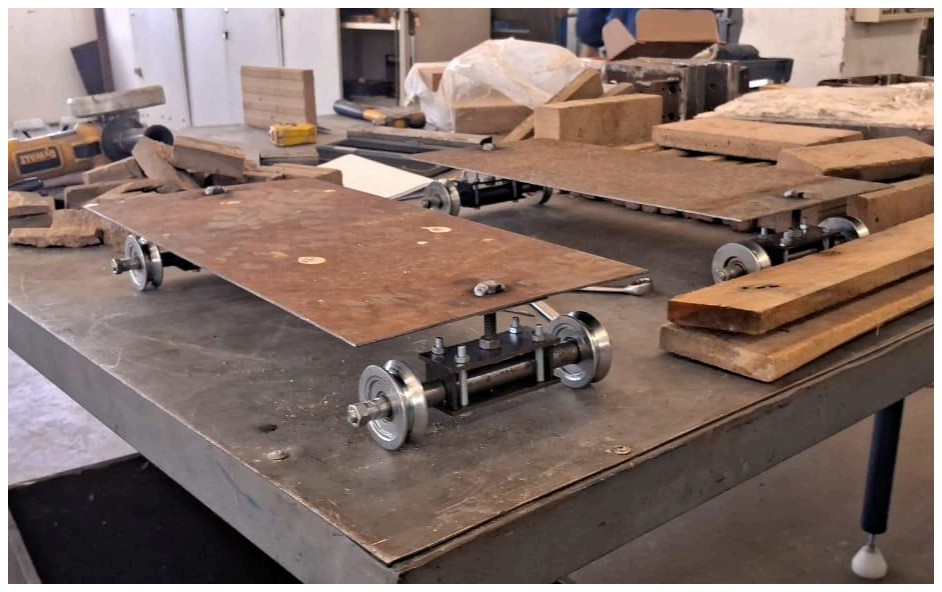
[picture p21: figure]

Fonte: Autoria própria (2025)

### 5.9. Dia 3 de dezembro

Os suportes para as resistências foram assentados com argamassa de para tijolos refratários nas laterais internas do forno, estes mesmos suportes tiveram que ser reposicionados na semana seguinte pois não aderiram corretamente a parede.
A fonte e a contactora foram montadas no painel elétrico.

Fig 35 .Forno com suporte resistências assentados

Fonte: Autoria própria (2025)

Fig 36 . Painel com fonte e contactor

Fonte: Autoria própria (2025)

### 5.10. Dia 10 de dezembro

Os suportes laterais foram reassentados na parede com sucesso.

Fig 37 . Suportes reposicionados

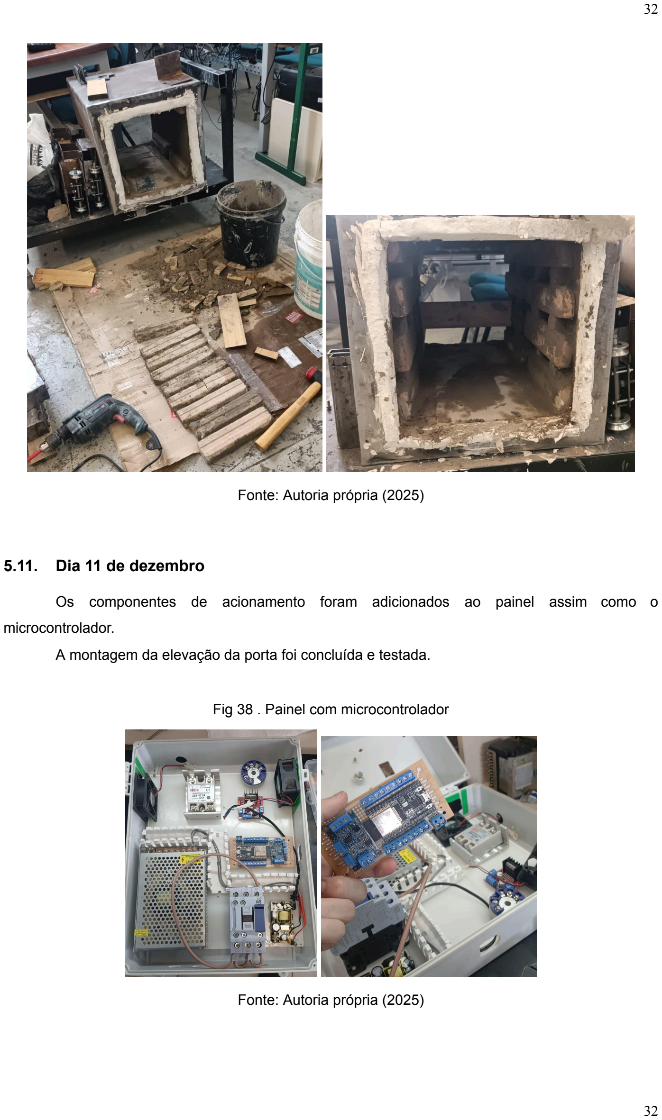
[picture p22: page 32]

Fonte: Autoria própria (2025)

### 5.11. Dia 11 de dezembro

Os componentes de acionamento foram adicionados ao painel assim como o microcontrolador.
A montagem da elevação da porta foi concluída e testada.

Fig 38 . Painel com microcontrolador

Fonte: Autoria própria (2025)

Fig 39 . Teste da elevação da porta

Fonte: Autoria própria (2025)

### 5.12. Dia 15 de dezembro

O painel foi ligado e testado utilizando uma resistência coleira a fim de representar a resistência real.
Fig 40 . Teste da elétrica com resistência coleira

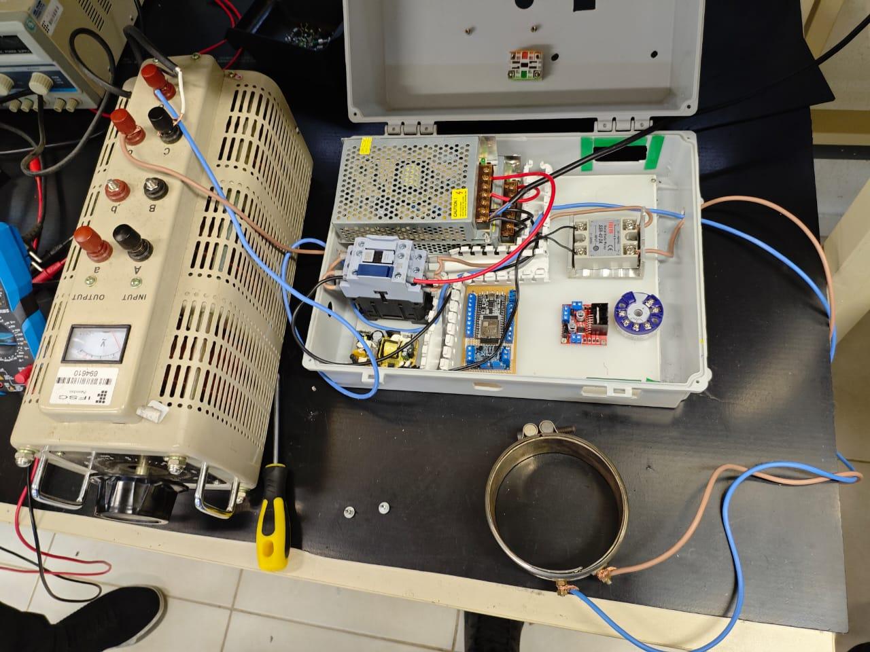
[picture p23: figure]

Fonte: Autoria própria (2025)

### 5.13. Dia 16 de dezembro

O forno foi colocado na mesa e a resistência foi posicionada nos vãos do suporte, em seguida as paredes foram furadas para acomodar os isoladores cerâmicos que fazem os pontos de acesso externo da resistência e para o termopar.

Fig 41 . Forno com espiras e conectores da resistência

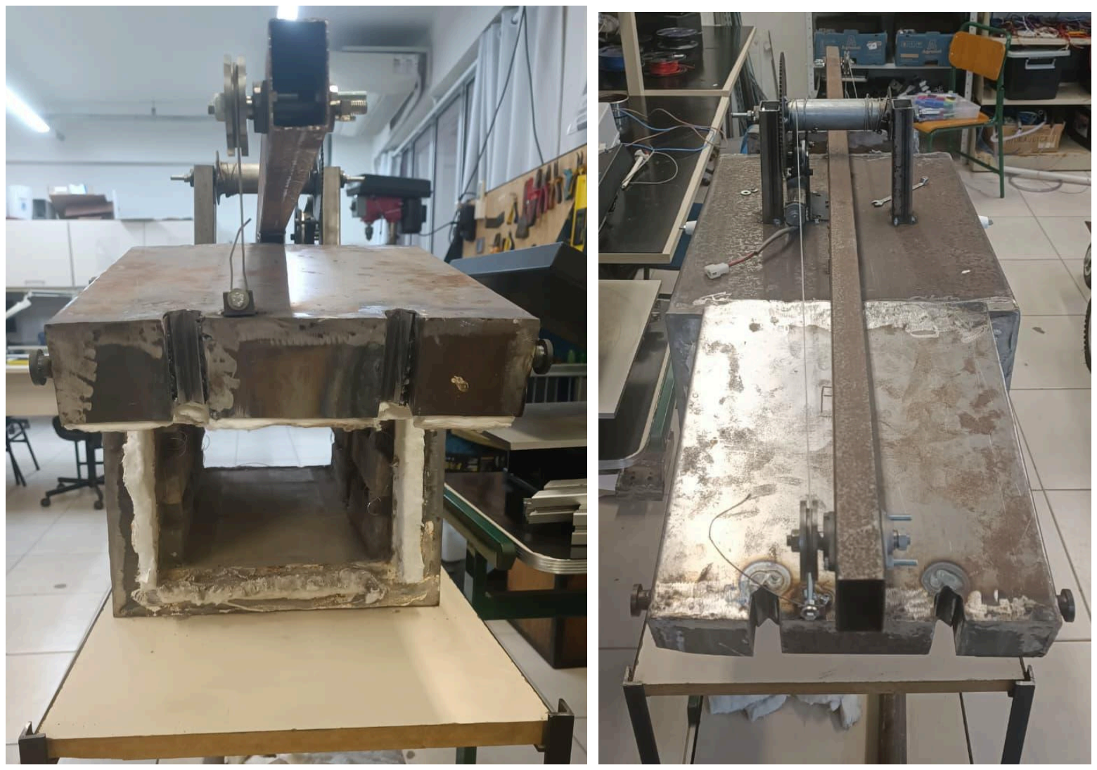
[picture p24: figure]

Fonte: Autoria própria (2025)

### 5.14. Dia 17 de dezembro

O mecanismo de travamento da porta foi instalado e o forno foi acionado pela primeira vez onde apresentou uma temperatura em torno dos 170ºc, foi evidenciado que o forno apresentava um grande vazamento térmico devido a falhas no isolamento térmico. Após o ocorrido o forno foi virado e as portas foram removidas o isolamento no encaixe da porta foi refeito e foram adicionados tijolos refratários no topo do forno.
Fig 42 . Primeiro teste de aquecimento do forno

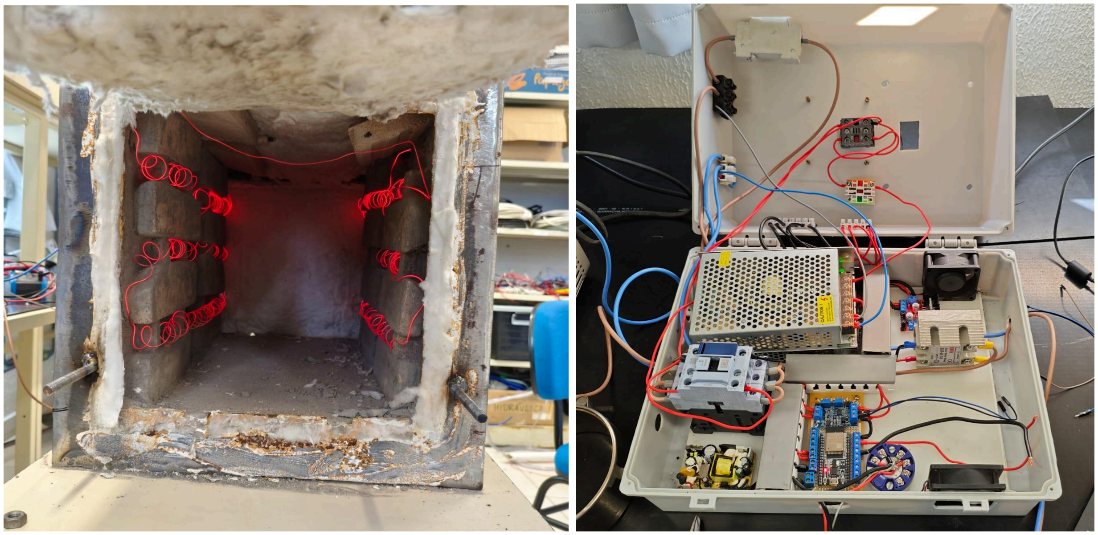
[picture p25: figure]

Fonte: Autoria própria (2025)

Fig 43 . Adendos na isolação

Fonte: Autoria própria (2025)

### 5.15. Dia 18 de dezembro

Após alguns retoques rápidos na isolação o forno foi ligado por aproximadamente uma hora e atingiu uma temperatura de aproximadamente 320ºC, porém o teste foi interrompido por uma falha em um componente externo e devido ao elevado tempo para realização dos testes não foi possível elevar a temperatura adiante. Com o forno frio os recém adicionados tijolos do topo do forno foram fixados utilizando argamassa refratária.

Fig 44 . Último teste do forno

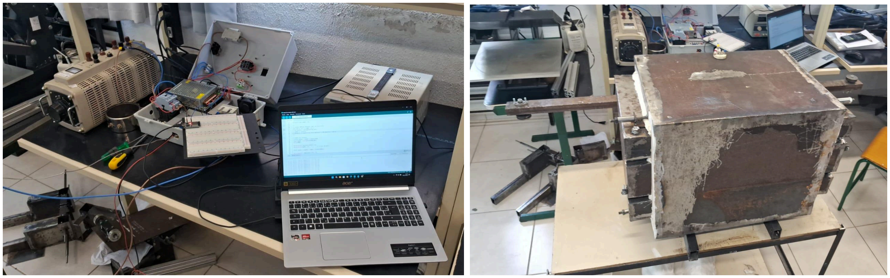
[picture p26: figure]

Fonte: Autoria própria (2025) Fig 45 . Topo fixado com argamassa

Fonte: Autoria própria (2025)

### 6. Resultados

Com a vedação térmica realizada, o forno apresentou comportamento térmico significativamente melhorado: partindo de uma temperatura interna de aproximadamente 30 °C, a ‘câmara alcançou cerca de 320 °C em torno de uma hora de aquecimento. Esse resultado indica uma redução das perdas por convecção e condução em relação às medições iniciais, quando vazamentos no isolamento permitiam que a temperatura máxima alcançada fosse substancialmente menor. A curva de aquecimento observada sugere que a distribuição de calor no interior da câmara tornou-se mais previsível e que o conjunto de isolamento e refratários, após os ajustes, passou a formar uma barreira térmica eficaz para os ensaios de curta duração realizados até o momento.
A aquisição e o condicionamento do sinal de temperatura mostraram-se adequados para monitoramento do processo: o termopar (tipo K) acoplado ao transmissor HT-010 e ao condicionador HW-685 forneceu leituras coerentes com o perfil de aquecimento registrado. Durante os testes a leitura do sensor manteve resposta consideravelmente estável e compatível com a variação de potência aplicada, permitindo reconstruir a evolução temporal da temperatura com resolução esperada para avaliação experimental. Salienta-se, no entanto, a necessidade de uma calibração fina e de verificação da linearidade em toda a faixa de interesse caso se realizem ensaios a temperaturas mais elevadas ou com requisitos de controle.

No âmbito do sistema de acionamento, a movimentação das portas do forno foi readaptada: com a nova configuração, o conjunto motorizado realiza os movimentos de subida e descida por pivotagem conforme o comando, sendo a ponte H (L293n) o elemento responsável pelo controle do sentido de giro e pela proteção básica do circuito.
Quanto ao painel de controle, constatou-se que todos os módulos integrados (interfaces de controle, sinais de atuação e leitura de sensores) estão funcionalmente operantes; entretanto, o painel ainda não foi fixado de forma definitiva à bancada de trabalho. A ausência de fixação permanente compromete a robustez das conexões e a ergonomia do sistema durante ensaios prolongados, podendo introduzir variabilidade nas leituras por movimentação dos cabos e vibrações. Por fim, a soldagem dos trilhos destinados à passagem dos carrinhos não foi executada devido a imprevistos acumulados ao longo do semestre, o que impediu a realização de ensaios em regime mais próximo ao operacional. A ausência dessa etapa estrutural limita a capacidade de testar transporte de peças dentro do forno sob condições reais, mas não compromete a verificação funcional dos subsistemas elétricos e térmicos já mencionados.

### 7. Conclusão

A execução do projeto permitiu a integração prática de conceitos iniciais de instrumentação, acionamento eletromecânico e controle térmico aplicados à fabricação de tijolos cerâmicos. Ao longo do desenvolvimento foram realizados cálculos necessários ao dimensionamento (redução de escala, dimensionamento de motor e resistência), seleção de componentes (termopar tipo K, transmissor HT-010, condicionador HW-685, SSR-40DA, ponte H L293n, motores Mabuchi e ESP 32) e construção das partes mecânicas e elétricas do protótipo.

Nos ensaios iniciais realizados em dezembro de 2025 verificou-se o comportamento térmico e de vedação do forno: no primeiro acionamento (17/12/2025) a temperatura alcançada foi da ordem de 170 °C, evidenciando vazamentos térmicos que motivaram intervenções no isolamento; após correções e reforço dos tijolos refratários o forno atingiu aproximadamente 320 °C em cerca de 1 hora, partindo de 30 °C (teste interrompido em 18/12/2025 por falha de um componente externo). Ademais, as soluções de automação propostas mostraram-se operacionais — as portas foram acionadas com sucesso via a ponte H e o circuito de controle — embora alguns itens de finalização, como a soldagem dos trilhos para passagem dos carrinhos e a fixação definitiva do painel, permaneçam pendentes.

Em suma, o protótipo desenvolvido demonstra um progresso técnico e oferece uma base para a evolução do sistema rumo a um forno elétrico automatizado industrialmente aplicável. Os resultados parciais obtidos confirmam que, com ajustes no isolamento, testes prolongados e implementação do controle fechado, no futuro, a solução proposta tem potencial para reduzir perdas por defeitos, aumentar a qualidade dos produtos e viabilizar economicamente a substituição parcial ou total de fornos a combustíveis fósseis manuais na olaria estudada.

### Referências Bibliográficas

[1] PUTTI, Eduardo Paz; FREITAS, João Emiliano Helrighel; DETTENBORN, Gabriel; LOBATO, Raian. AE1
Tijolos | – | MPP. | Disponível | em:
https://github.com/EduardoPaz01/AE-Tijolos/blob/main/AE1%20Tijolos%20-%20MPP.pdf. Acesso em: 17 dez. 2025.
[2] L. Lima, “Custos na produção de tijolos e análise do preço de venda: um estudo de caso”, Santa Maria, RS, Brasil, 2004.
[3] DOEBELIN, Ernest O. Measurement systems: application and design. 4. ed. New York: McGraw-Hill, 1990.
Disponível | em:
https://physicsinstrumentation.wordpress.com/wp-content/uploads/2015/03/measurement_systems_application_design.pdf. Acesso em: 18 dez. 2025.
[4] MERCADO LIVRE. Termopar tipo K cerâmico 1300ºC 215 mm p/ forno forja. Disponível em: https://produto.mercadolivre.com.br/MLB-1978235499-termopar-tipo-k-cermico-1300c-215mm-p-forno-forja-_JM. Acesso em: 18 dez. 2025.
[5] INTERNATIONAL ELECTROTECHNICAL COMMISSION. IEC 60584-1: Thermocouples – Part 1: EMF
specifications | and | tolerances. | Edition | 3.0. | Geneva: | IEC, | 2013. | Disponível | em:
https://cdn.standards.iteh.ai/samples/18205/94ad5627a504499e94f8a247c744934d/IEC-60584-1-2013.pdf. Acesso em: 18 dez. 2025.
[6] TEXAS INSTRUMENTS. SBAA274A – A Basic Guide to Thermocouple Measurements. Dallas: Texas Instruments, 2020. Disponível em: https://www.ti.com/lit/an/sbaa274a/sbaa274a.pdf. Acesso em: 18 dez. 2025.
[7] | SALVI | CASAGRANDE. | Transmissor | de | temperatura | HT-010. | Disponível | em:
https://www.salvicasagrande.com.br/produto/transmissor-de-temperatura-ht-010/113/31. Acesso em: 18 dez. 2025.
[8] TEKNIMAS. Conversor Termopar K/J PT100 programável USB 4-20mA HT-010. Disponível em: https://loja.teknimas.com.br/conversor-termopar-k-j-pt100-programavel-usb-4-20ma-ht-010. Acesso em: 18 dez. 2025.
[9] | CONNECT | JCO. | Transmissor | de | temperatura | modelo | CJTM-08. | Disponível | em:
https://www.connectjco.com.br/produtos/temperatura/transmissor-de-temperatura-modelo-cjtm-08/. Acesso em: 18 dez. 2025.
[10] BBIRI CENTRE. HW685 – Current to Voltage Module (0-4/20mA to 0-3.3V/5V/10V Voltage Transmitter).
Disponível | em:
https://www.bbiri-centre.com/product-page/hw685-current-to-voltage-module-0-4-20ma-to-0-3-3v5v10v-voltag e-transmitter-sign. Acesso em: 18 dez. 2025.

[11] MREECO. Current to Voltage Module HW-685 (0-4/20mA to 0-3.3V/5V/10V Voltage Transmitter). Disponível em: https://mreeco.com/products/current-to-voltage-module-hw-685-637721594534307690. Acesso em: 18 dez. 2025.
[12] | DIGILOG. | Current | to | Voltage | Module | in | Pakistan | (HW-685). | Disponível | em:
https://digilog.pk/products/current-to-voltage-module-in-pakistan-www-hallroad-org. Acesso em: 18 dez. 2025.
[13] UELECTRONICS. HW-685 – Módulo convertidor corriente a voltaje. Disponível em: https://uelectronics.com/producto/hw-685-modulo-convertidor-corriente-a-voltaje/. Acesso em: 18 dez. 2025.
[14] ARDUCORE. Relé de estado sólido SSR-40DA 40A 250V 3-32V. Disponível em: https://www.arducore.com.br/rele-de-estado-solido-ssr-40da-40a-250v-3-32v. Acesso em: 18 dez. 2025.
[15] | DATASHEET | CAFE. | SSR-40DA | – | Solid | State | Relay | datasheet. Disponível em:
https://www.datasheetcafe.com/ssr-40da-pdf-23046/. Acesso em: 18 dez. 2025.
[16] TEXAS INSTRUMENTS. L293 – Quadruple Half-H Drivers. Datasheet. Dallas: Texas Instruments, 2000. Disponível em: https://www.ti.com/lit/ds/symlink/l293.pdf. Acesso em: 18 dez. 2025.
[17] ELETROGATE. Ponte H dupla L298N. Disponível em: https://www.eletrogate.com/ponte-h-dupla-l298n. Acesso em: 18 dez. 2025.
[18] | ELETROGATE. | Guia | definitivo | de | uso | da | Ponte | H | L298N. | Disponível | em:
https://blog.eletrogate.com/guia-definitivo-de-uso-da-ponte-h-l298n/. Acesso em: 18 dez. 2025.
[19] MERCADO LIVRE. Motor de vidro elétrico Mabuchi 12V 8 dentes lado direito. Disponível em: https://www.mercadolivre.com.br/motor-de-vidro-eletrico-mabuchi-12v-8-dentes-lado-direito/up/MLBU3496517048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. Acesso em: 18 dez. 2025.
[20] FITZGERALD, A. E.; KINGSLEY Jr., C.; UMANS, S. D. Máquinas Elétricas. McGraw-Hill. [21]LINGFRAN. 220V Variac Variable Transformer – Autotransformador variável. Disponível em: https://pt.lingfran.com/transformers/variable-autotransformer/220v-variac-variable-transformer.html. Acesso em: 18 dez. 2025.
[22] MERCADO LIVRE. Fonte chaveada 20A 12V 240W bivolt colmeia CFTV fita LED. Disponível em: https://www.mercadolivre.com.br/fonte-chaveada-20a-12v-240w-bivolt-colmeia-cftv-fita-led/p/MLB27797583. Acesso em: 18 dez. 2025.
[23] MERCADO LIVRE. Kit 10 fonte de alimentação bivolt 5V 2A P4. Disponível em: https://produto.mercadolivre.com.br/MLB-2746179030-kit-10-fonte-de-alimentaco-bivolt-5v-2a-p4-_JM. Acesso em: 18 dez. 2025.
[24] | ELETROGATE. | Módulo | WiFi | ESP | 32 | Bluetooth | 30 | pinos. | Disponível | em:
https://www.eletrogate.com/modulo-wifi-esp32-bluetooth-30-pinos. Acesso em: 18 dez. 2025.
[25] R. L. Mott, Machine elements in mechanical design, 4th ed. Upper Saddle River, N.J: Pearson/Prentice Hall, 2004.
[26] Curso de física básica 1: mecânica. Editora Edgard Blucher, 2022

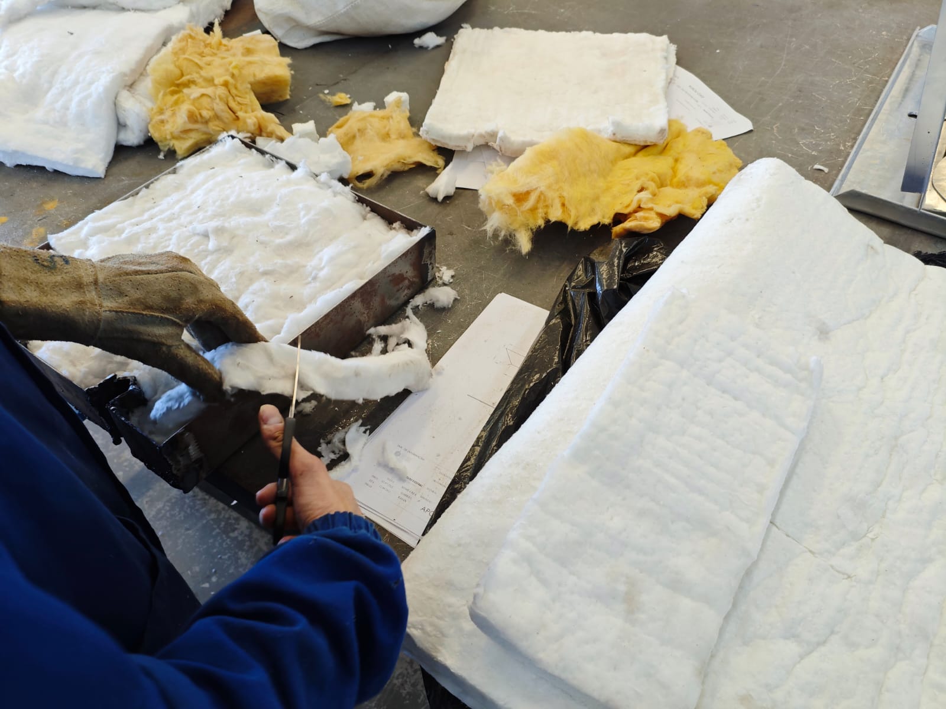
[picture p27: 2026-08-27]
AE-II/AE2 - imagens relatório/set - 25 de setembro/inserindo isolação na porta.jpeg

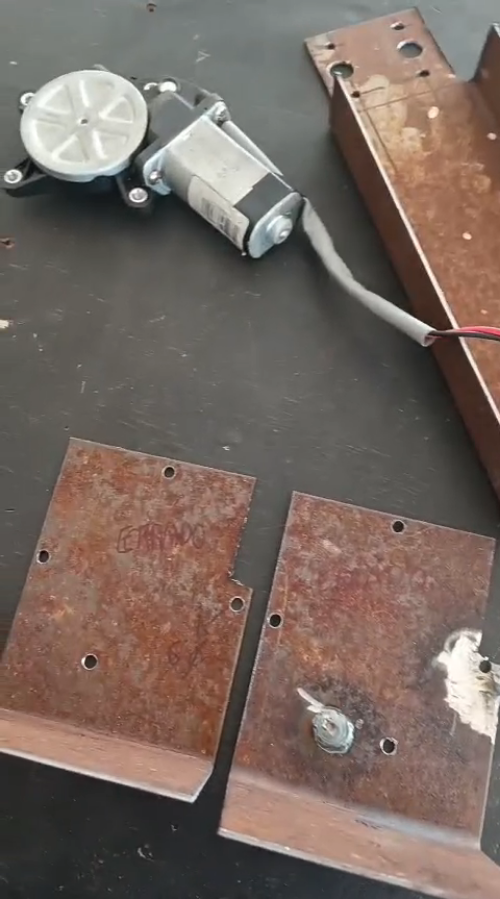
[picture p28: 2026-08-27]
AE-II/AE2 - imagens relatório/out - 14 de outubro/suporte do motor errado.png

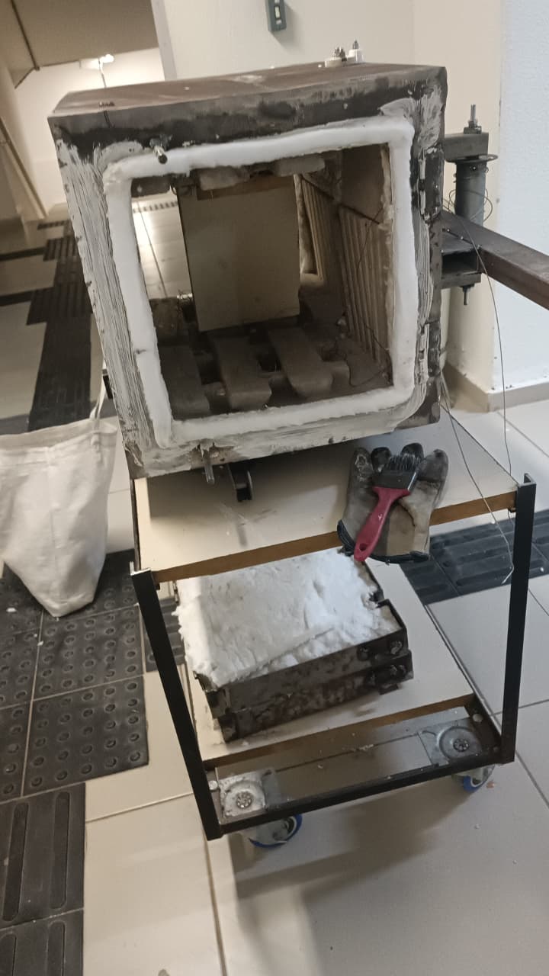
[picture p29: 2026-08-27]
AE-II/AE2 - imagens relatório/dez - 17 de dezembro/forno virado para colocar isolação no teto.jpeg

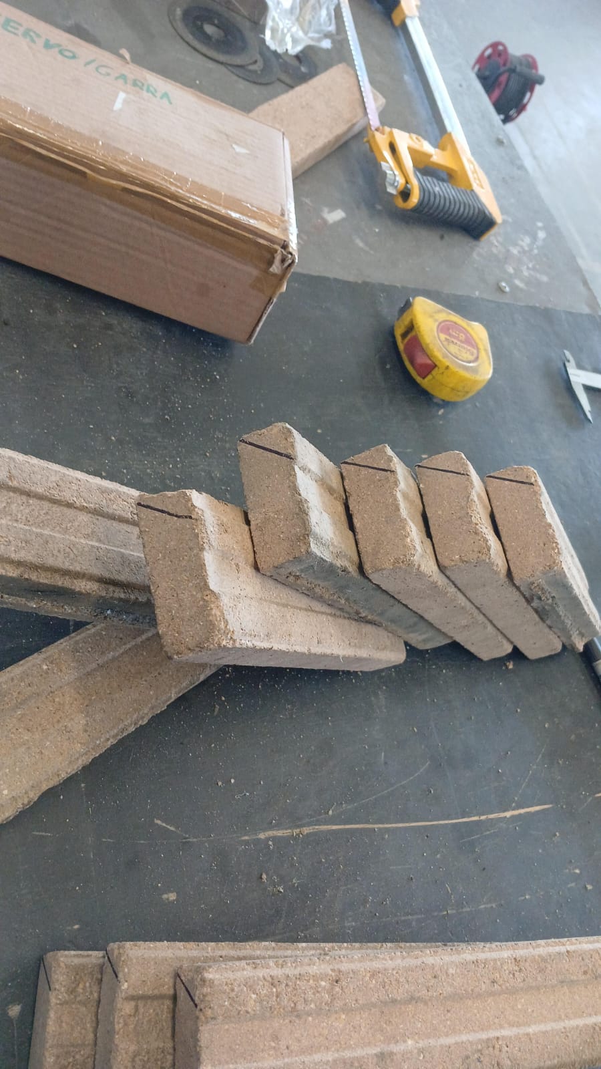
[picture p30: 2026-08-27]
AE-II/AE2 - imagens relatório/nov - 27 de novembro/corte de tijolos.jpeg

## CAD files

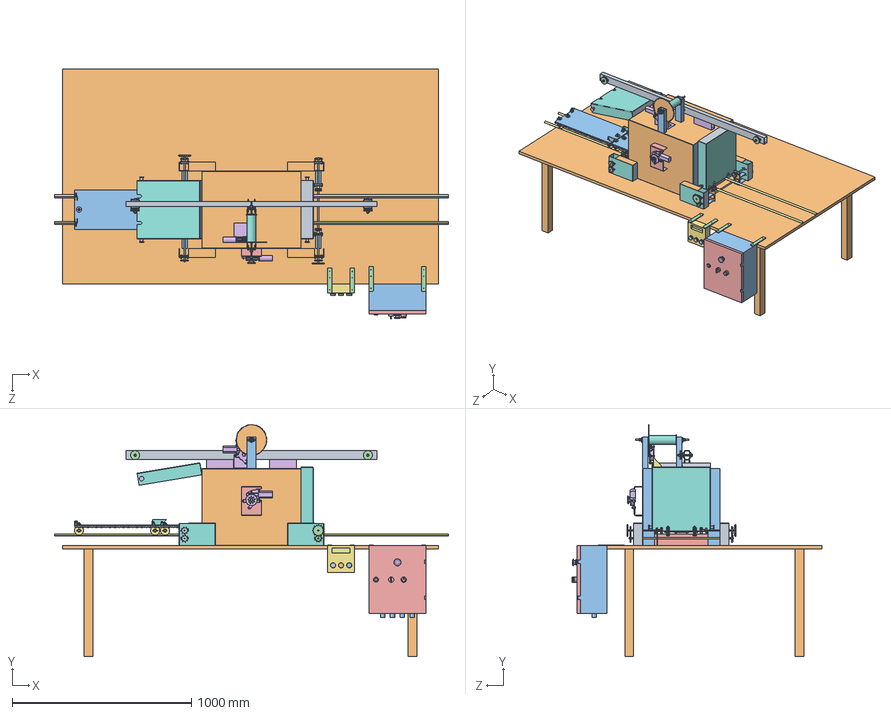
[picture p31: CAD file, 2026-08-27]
AE-II/REVISAO - AE2 - Tijolos Projeto mecânico/CARRINHO/FORNO/Montagens/FNR-00-04-01.SLDASM
2200.0 x 1297.1 x 1393.5 mm
FNR-01-02-02
FNR-01-02-01
FNR-01-01-01 x 4
FNR-01-01-02 x 2
FNR-01-01-03 x 2
FNR-01-03-01 x 12
FNR-01-03-02 x 4
FNR-01-03-03 x 4
FNR-01-03-04 x 2
FNR-01-03-05
FNR-01-03-06 x 4
FNR-01-03-07 x 2
FNR-01-04-01 x 2
FNR-01-05-01 x 12
REF-01-00-00 x 8
POR_01_00_00 x 2
POR_01_00_01 x 2
POR_01_00_07 x 4
POR_01_00_08 x 2
POR_01_00_09 x 8
POR_01_00_10 x 4
POR_01_00_04 x 4
POR_01_00_11 x 6
SPM-00-00-01 x 8
MC.00.00.01 x 19
CSS-00-00-02 x 8
radial ball bearing_68_din x 8
european type roller chain wheel_s_din x 6
hex nut gradec_din x 16
hex screw gradec_din x 16
ETI-00-00-04 x 2
ENG-00-01-01 x 4
CSS-00-00-03 x 8
SUP_01_00_00 x 4
SUP_01_00_01 x 8
hex screw gradec_iso x 28
radial ball bearing_68_iso x 4
hex nut gradec_iso x 38
ESP_01_00_02 x 4
ETI-00-00-06 x 2
ENG-00-01-04 x 4
ETI-00-00-05 x 2
CAR_01_00_01 x 2
CAR_01_01_05 x 4
CAR_01_01_06 x 4
CAR_01_01_02 x 4
CAR_01_01_01 x 8
SKU_7360 x 8
split pin_din x 8
hex screw gradeab_iso x 16
hex nut style 1 gradeab_iso x 24
CAR_01_01_04 x 8
CAR_01_00_02 x 4
plain washer 10669 type nl_iso x 16
CAR_01_02_01 x 8
CAR_01_02_00 x 4
CAR_01_00_03 x 4
MSA-01-00-00
PNL-00-00-01
PNL-00-00-04 x 4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

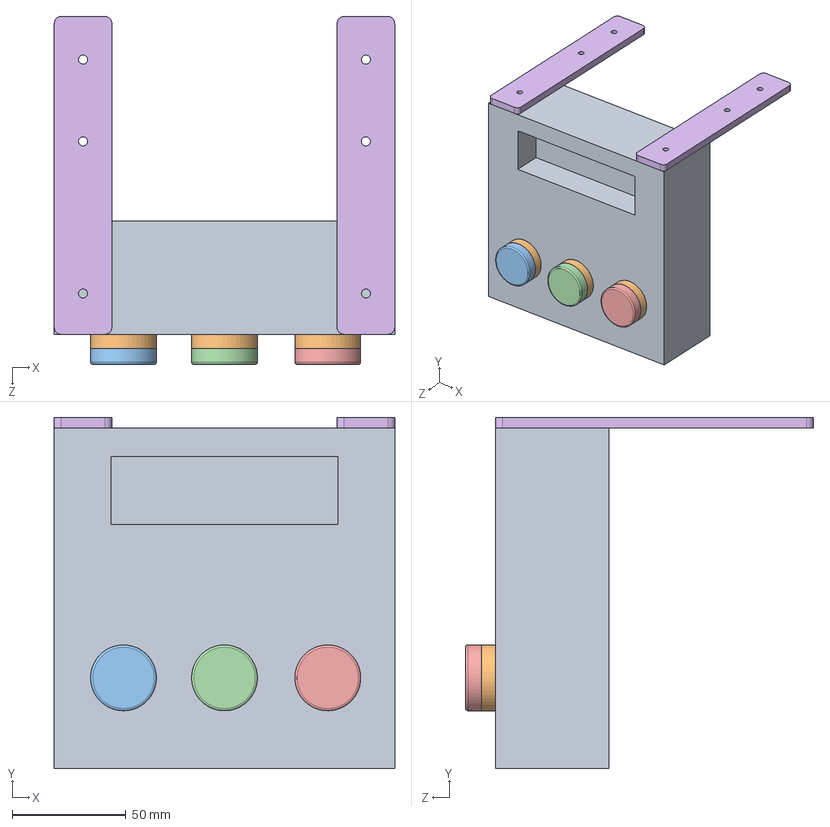
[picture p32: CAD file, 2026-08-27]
AE-II/REVISAO - AE2 - Tijolos Projeto mecânico/CARRINHO/IHM/MIHM-00-01-00.SLDASM
150.0 x 154.8 x 153.3 mm
IHM-00-00-04
IHM-00-00-01 x 3
IHM-00-00-03
IHM-00-00-02
IHM-00-00-00
PNL-00-00-04 x 2

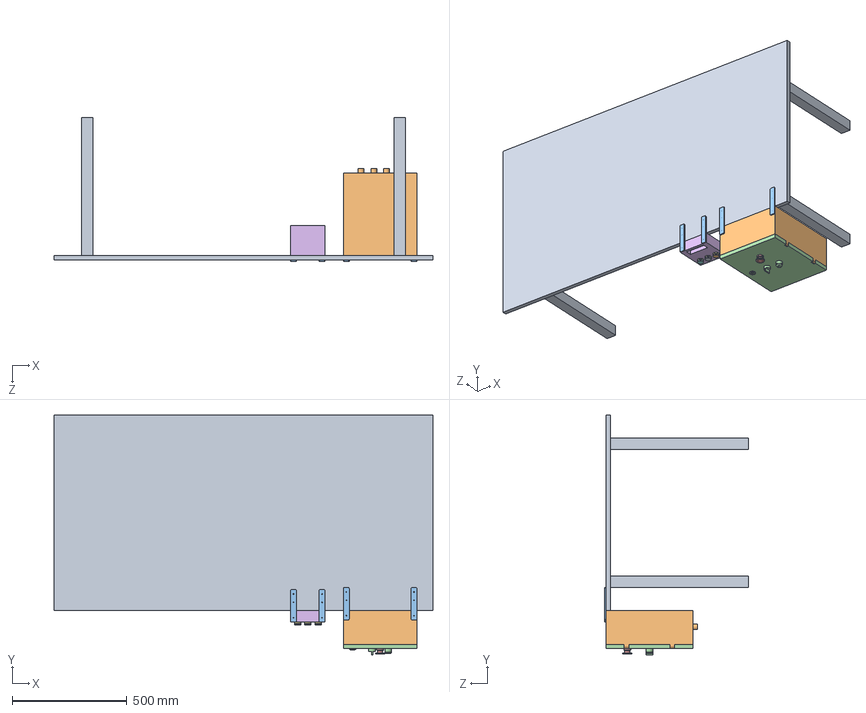
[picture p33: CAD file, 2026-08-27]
AE-II/REVISAO - AE2 - Tijolos Projeto mecânico/CARRINHO/MESA DE APOIO PRO FORNO/Montagem/MSA-00-00-00.SLDASM
1650.0 x 1043.5 x 624.8 mm
MSA-01-00-00
PNL-00-00-01
PNL-00-00-04 x 4
PNL-00-00-00
PNL-00-00-05
IHM-00-00-04
IHM-00-00-01 x 3
IHM-00-00-03
IHM-00-00-02
IHM-00-00-00

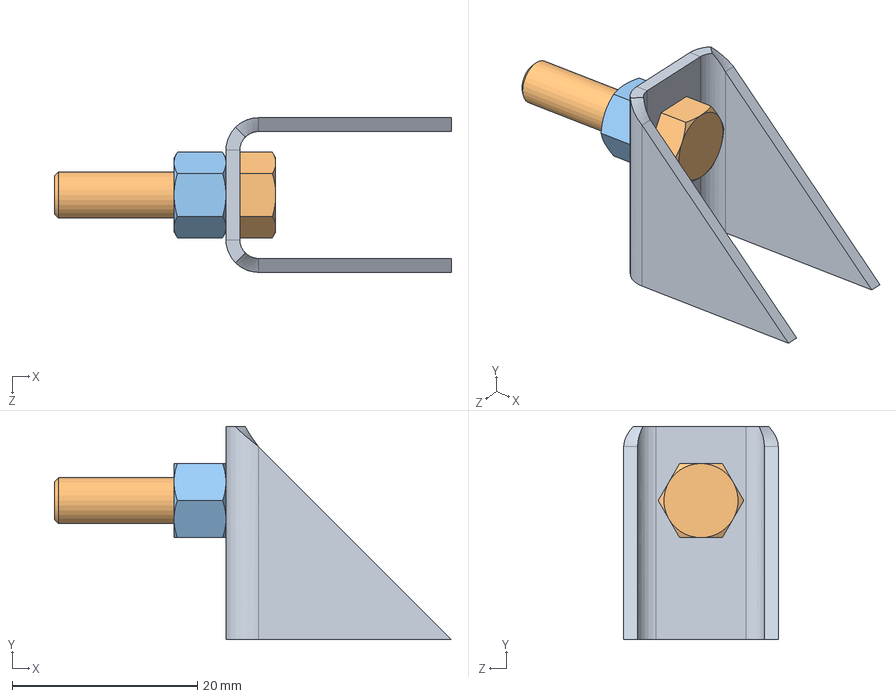
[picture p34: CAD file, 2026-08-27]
AE-II/REVISAO - AE2 - Tijolos Projeto mecânico/CARRINHO/Montagens/CAR_00_03_00.SLDASM
42.8 x 23.0 x 16.7 mm
CAR_01_02_01
hex screw gradec_iso
hex nut gradec_iso

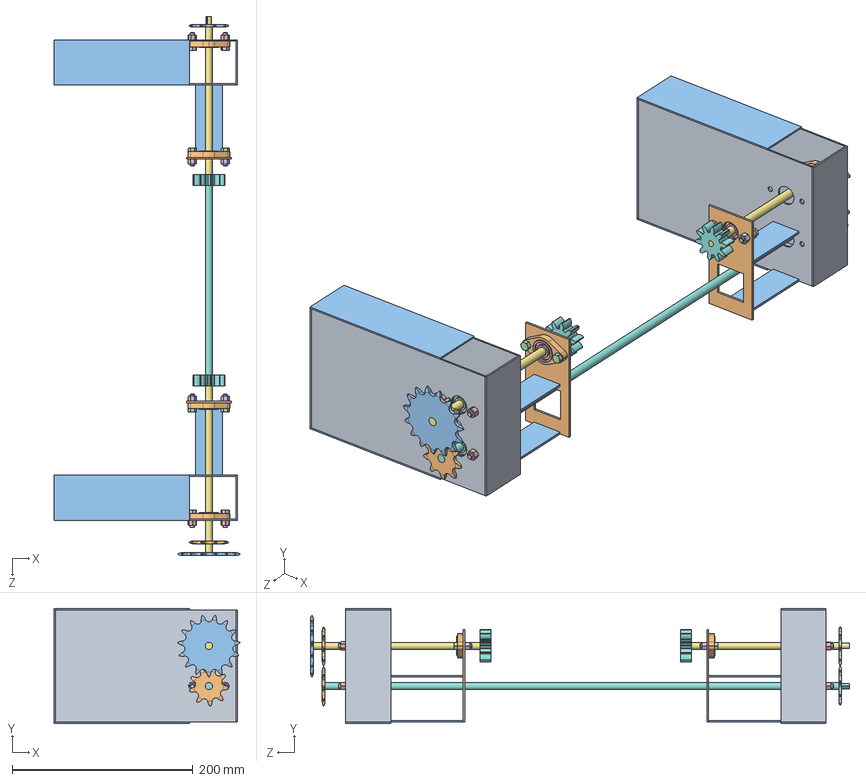
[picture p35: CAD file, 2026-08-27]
AE-II/REVISAO - AE2 - Tijolos Projeto mecânico/CARRINHO/MOVIMENTAÇÃO DO CARRINHO/Montagens/CT-00-00-00.SLDASM
205.9 x 127.5 x 597.0 mm
SPM-00-00-01 x 4
MC.00.00.01 x 6
CSS-00-00-02 x 4
radial ball bearing_68_din x 4
hex nut gradec_din x 8
hex screw gradec_din x 8
ETI-00-00-04
ENG-00-01-01 x 2
CSS-00-00-03 x 4
SUP_01_00_00 x 2
SUP_01_00_01 x 4
hex screw gradec_iso x 4
radial ball bearing_68_iso x 2
hex nut gradec_iso x 4
ETI-00-00-06
ETI-00-00-05
ENG-00-01-04 x 2
ENG-00-01-05 x 2
ENG-00-01-03

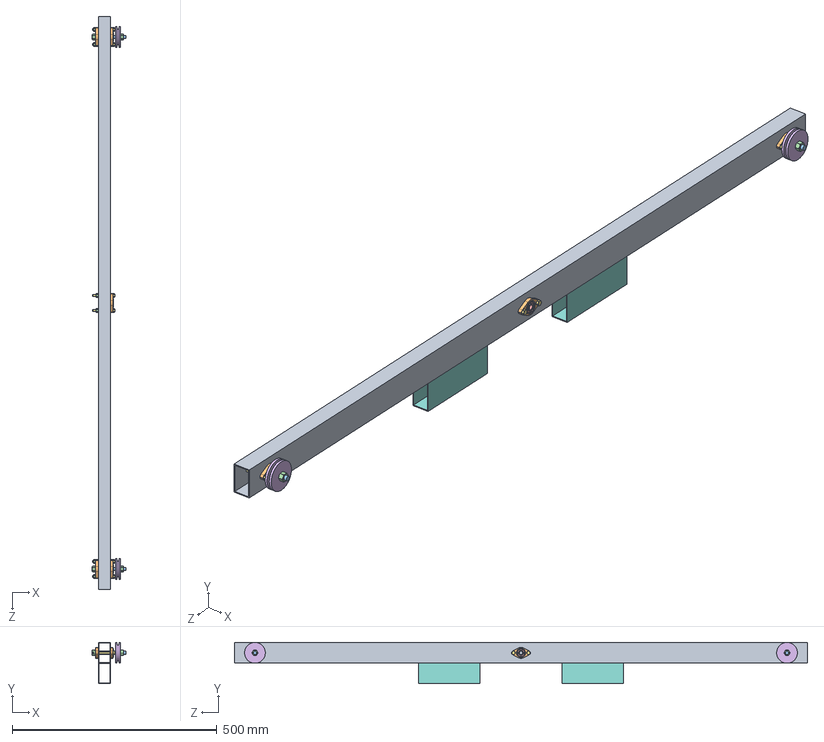
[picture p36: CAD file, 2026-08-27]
AE-II/REVISAO - AE2 - Tijolos Projeto mecânico/CARRINHO/PORTA FORNO/montagem/POR_00_04_00.SLDASM
82.0 x 100.4 x 1400.0 mm
POR_01_04_00
MC.00.00.01 x 5
POR_01_04_02 x 2
hex nut gradec_iso x 10
radial ball bearing_68_skf x 5
POR_01_04_01 x 2
hex bolt gradec_iso x 6
POR_01_04_03 x 2

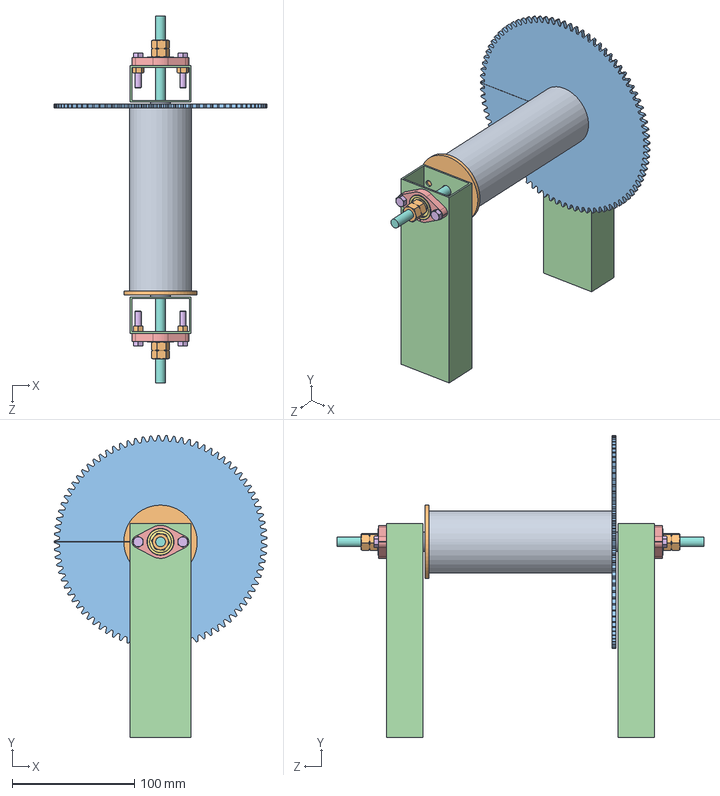
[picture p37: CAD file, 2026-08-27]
AE-II/REVISAO - AE2 - Tijolos Projeto mecânico/CARRINHO/TAMBOR/Montagens/TAM_00_00_00.SLDASM
174.0 x 247.0 x 300.0 mm
TAM_01_00_00
TAM_01_00_01
TAM_01_00_02
TAM_01_00_03 x 2
MC.00.00.01 x 2
hex bolt gradec_iso x 4
radial ball bearing_68_skf x 2
TAM_01_00_04
plain washer normal grade c_iso x 2
hex nut style 1 gradeab_iso x 8

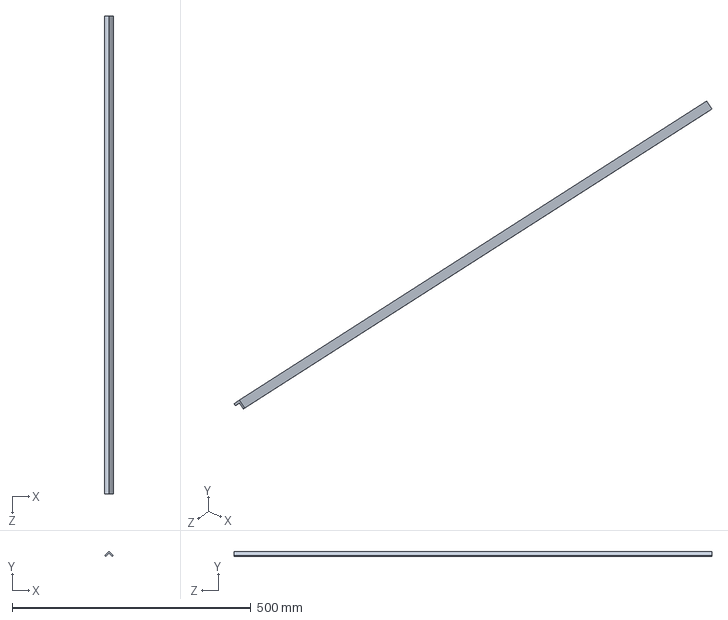
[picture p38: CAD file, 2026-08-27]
AE-II/REVISAO - AE2 - Tijolos Projeto mecânico/CARRINHO/TRILHO/Montagem/TRI_00_00_00.SLDASM
18.0 x 11.2 x 1000.0 mm

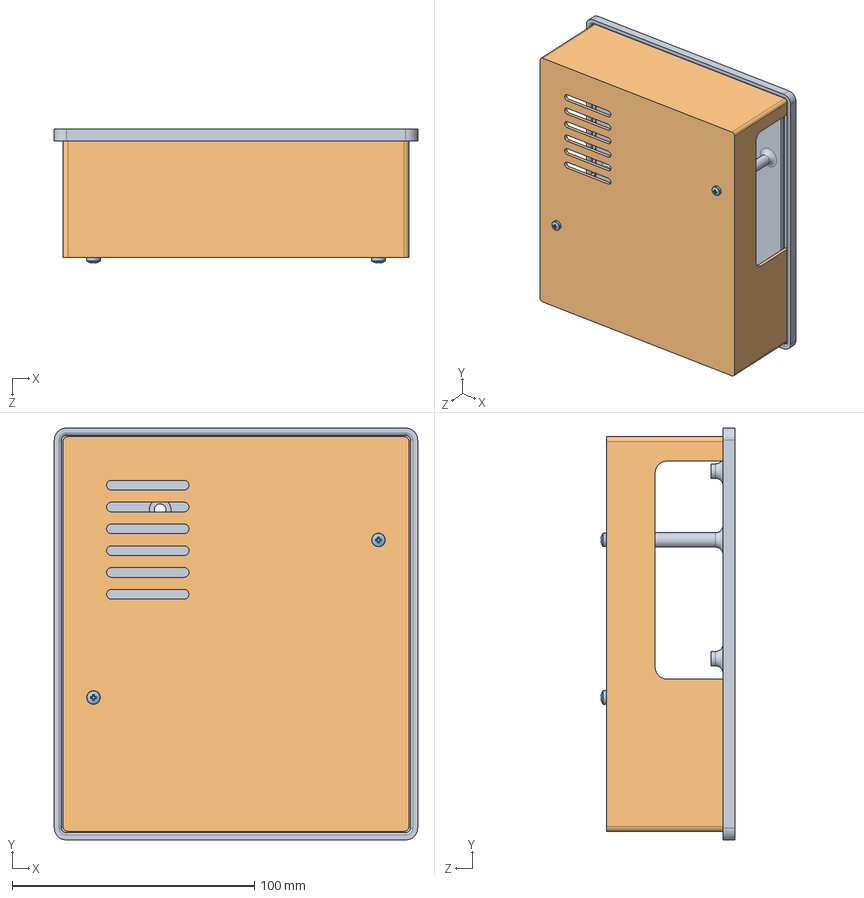
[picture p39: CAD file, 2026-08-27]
AE-III/Mecânica/Montagem_Caixa_Processador.SLDASM
150.0 x 170.0 x 55.4 mm
Base_Caixa_Processsador
tampa_Caixa_Processsador
pan head cross recess screw_iso x 2

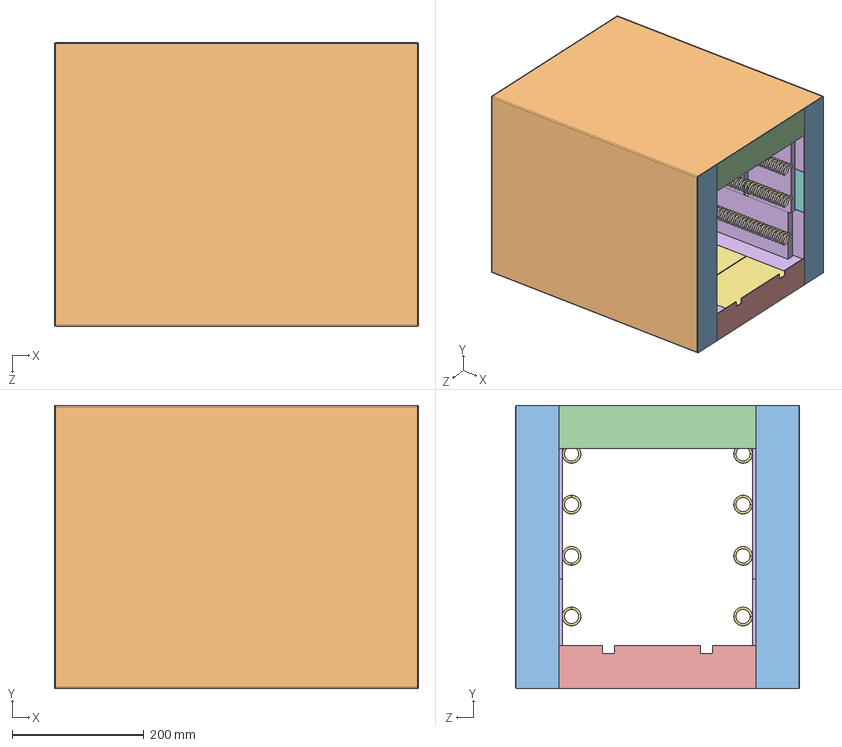
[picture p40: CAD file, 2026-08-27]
AE-II/REVISAO - AE2 - Tijolos Projeto mecânico/CARRINHO/FORNO/Montagens/FNR-00-03-01.SLDASM
553.0 x 430.1 x 432.1 mm
FNR-01-02-02
FNR-01-02-01
FNR-01-01-01 x 4
FNR-01-01-02 x 2
FNR-01-01-03 x 2
FNR-01-03-01 x 12
FNR-01-03-02 x 4
FNR-01-03-03 x 4
FNR-01-03-04 x 2
FNR-01-03-05
FNR-01-03-06 x 4
FNR-01-03-07 x 2
FNR-01-04-01 x 2
FNR-01-05-01 x 12
REF-01-00-00 x 8

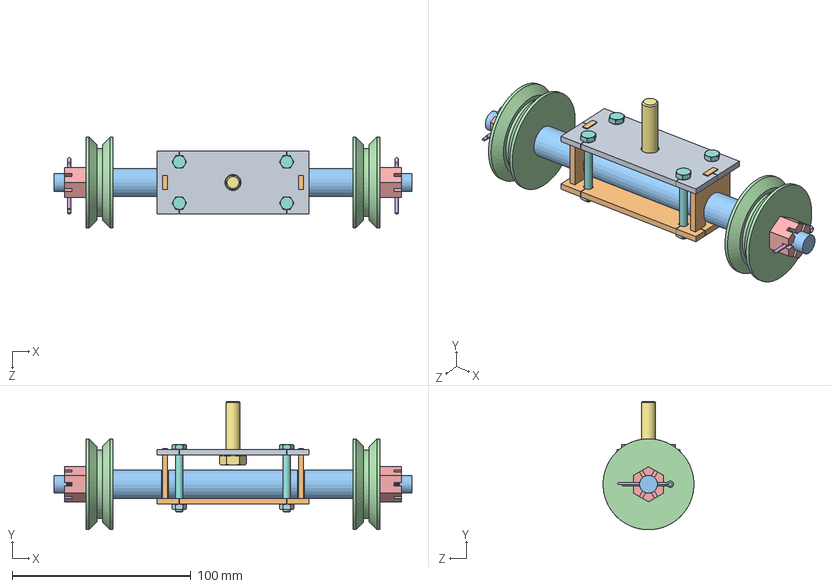
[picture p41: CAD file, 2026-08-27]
AE-II/REVISAO - AE2 - Tijolos Projeto mecânico/CARRINHO/Montagens/CAR_00_01_00.SLDASM
200.0 x 71.8 x 50.8 mm
CAR_01_01_05
CAR_01_01_06
CAR_01_01_02
CAR_01_01_01 x 2
SKU_7360 x 2
split pin_din x 2
hex screw gradec_iso
hex screw gradeab_iso x 4
hex nut style 1 gradeab_iso x 4
CAR_01_01_04 x 2

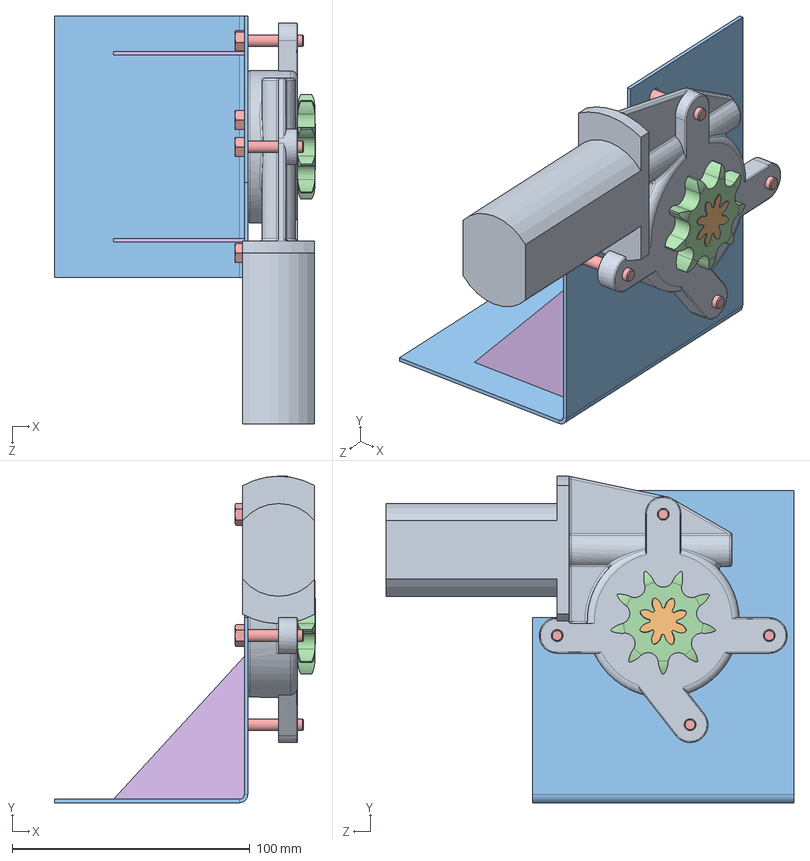
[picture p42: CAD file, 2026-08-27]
AE-II/REVISAO - AE2 - Tijolos Projeto mecânico/CARRINHO/MOTOR/LE.LC-578VA.SLDASM
109.8 x 137.3 x 171.6 mm
LE.LC-578VA_M
EN.LC-578VA
MTR.01.00.00
MTR.01.00.04
hex screw gradec_iso x 4
MTR.01.00.01 x 2

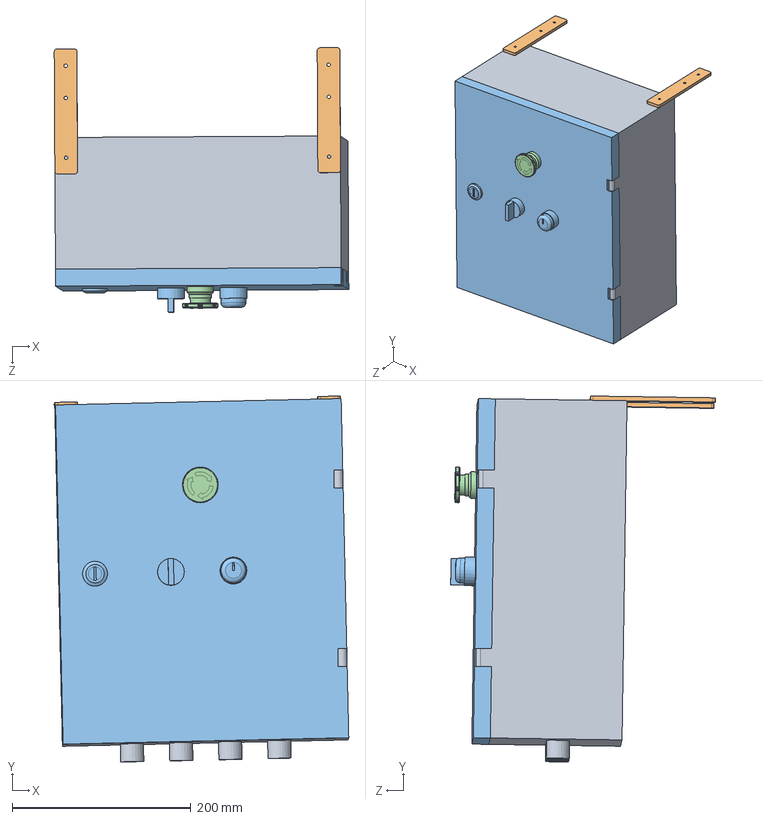
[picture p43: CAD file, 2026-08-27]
AE-II/REVISAO - AE2 - Tijolos Projeto mecânico/CARRINHO/PAINEL ELÉTRICO/PEÇAS E MONTAGEM/PNL-00-01-00.SLDASM
329.9 x 409.9 x 296.5 mm
PNL-00-00-01
PNL-00-00-04 x 2
PNL-00-00-00
PNL-00-00-05

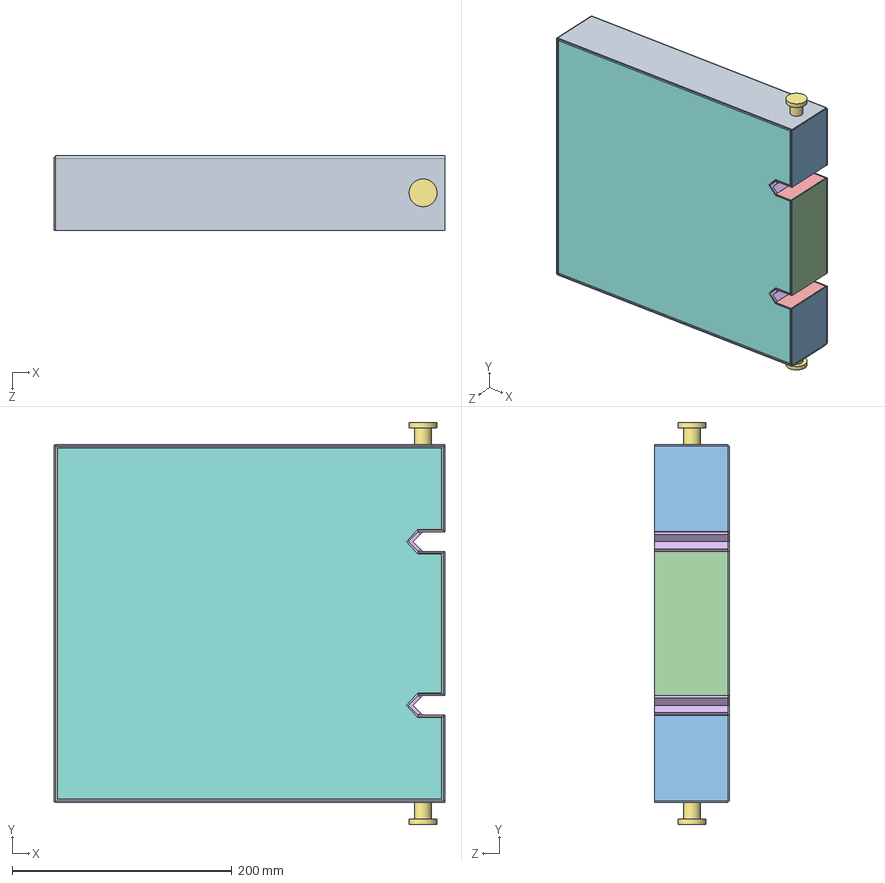
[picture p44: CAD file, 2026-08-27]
AE-II/REVISAO - AE2 - Tijolos Projeto mecânico/CARRINHO/PORTA FORNO/montagem/POR_00_00_00.SLDASM
356.2 x 366.5 x 68.5 mm
POR_01_00_00
POR_01_00_01
POR_01_00_07 x 2
POR_01_00_08
POR_01_00_09 x 4
POR_01_00_10 x 2
POR_01_00_04 x 2
POR_01_00_11 x 3

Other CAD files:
AE-II/REVISAO - AE2 - Tijolos Projeto mecânico/CARRINHO/MOVIMENTAÇÃO DO CARRINHO/Montagens/ESP_00_00_01.SLDASM
AE-II/REVISAO - AE2 - Tijolos Projeto mecânico/CARRINHO/FORNO/Montagens/FNR-00-00-01.SLDASM
AE-II/REVISAO - AE2 - Tijolos Projeto mecânico/CARRINHO/Montagens/CAR_00_02_00-E.SLDASM
AE-II/REVISAO - AE2 - Tijolos Projeto mecânico/CARRINHO/MOVIMENTAÇÃO DO CARRINHO/Montagens/ESP_00_00_02.SLDASM
AE-II/REVISAO - AE2 - Tijolos Projeto mecânico/CARRINHO/FORNO/Montagens/FNR-00-00-01.SLDDRW
AE-II/REVISAO - AE2 - Tijolos Projeto mecânico/CARRINHO/FORNO/Montagens/FNR-00-01-01.SLDASM
AE-II/REVISAO - AE2 - Tijolos Projeto mecânico/CARRINHO/FORNO/Montagens/FNR-00-01-01.SLDDRW
AE-II/REVISAO - AE2 - Tijolos Projeto mecânico/CARRINHO/FORNO/Montagens/FNR-00-02-01.SLDASM
AE-II/REVISAO - AE2 - Tijolos Projeto mecânico/CARRINHO/FORNO/Montagens/FNR-00-02-01.SLDDRW
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

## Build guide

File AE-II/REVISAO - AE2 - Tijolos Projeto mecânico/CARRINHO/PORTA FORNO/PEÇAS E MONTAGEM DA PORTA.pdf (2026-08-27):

5

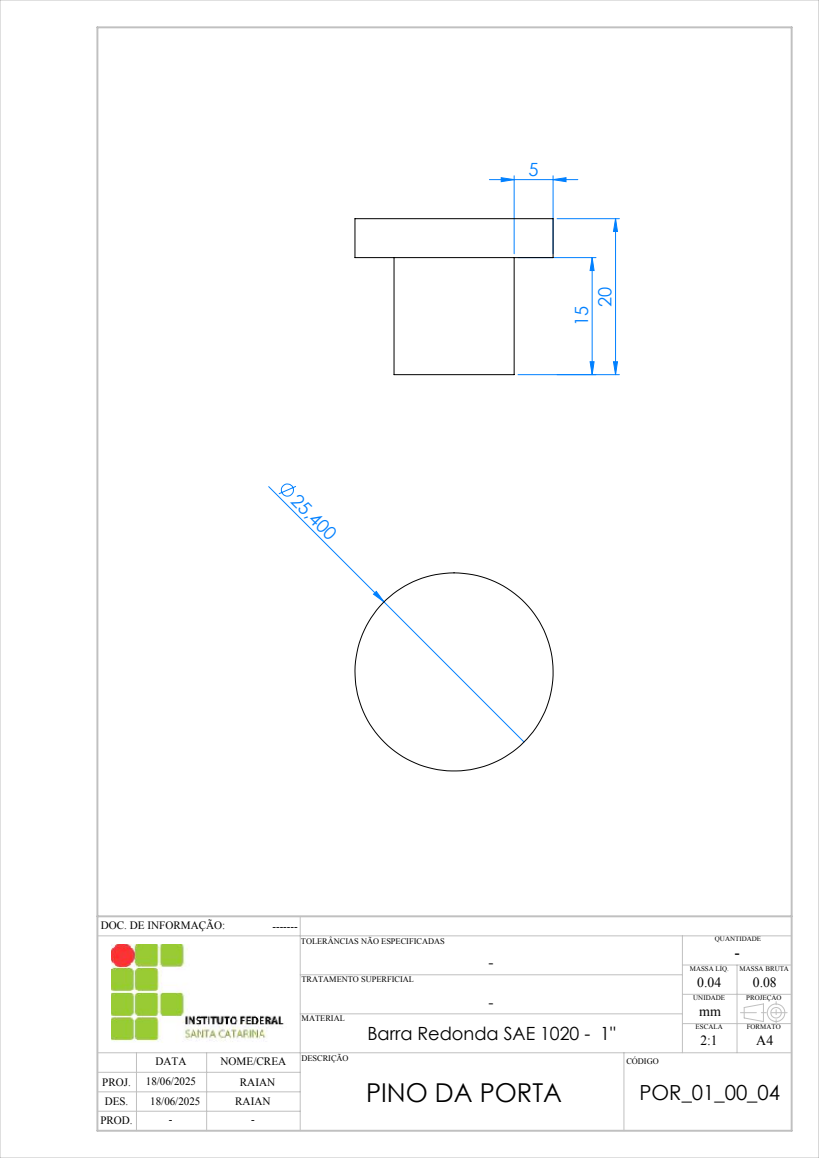
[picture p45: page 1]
PROJ. DES. PROD.; DATA; NOME/CREA DESCRIÇÃO; CÓDIGO; TRATAMENTO SUPERFICIAL; ESCALA; FORMATO; UNIDADE; MASSA LÍQ.; QUANTIDADE; RAIAN; POR_01_00_04 ¹⁸/06/2025; MASSA BRUTA 0.08; PROJEÇÃO

DOC. DE INFORMAÇÃO:

TOLERÂNCIAS NÃO ESPECIFICADAS

MATERIAL
Barra Redonda SAE 1020 - 1"
PINO DA PORTA

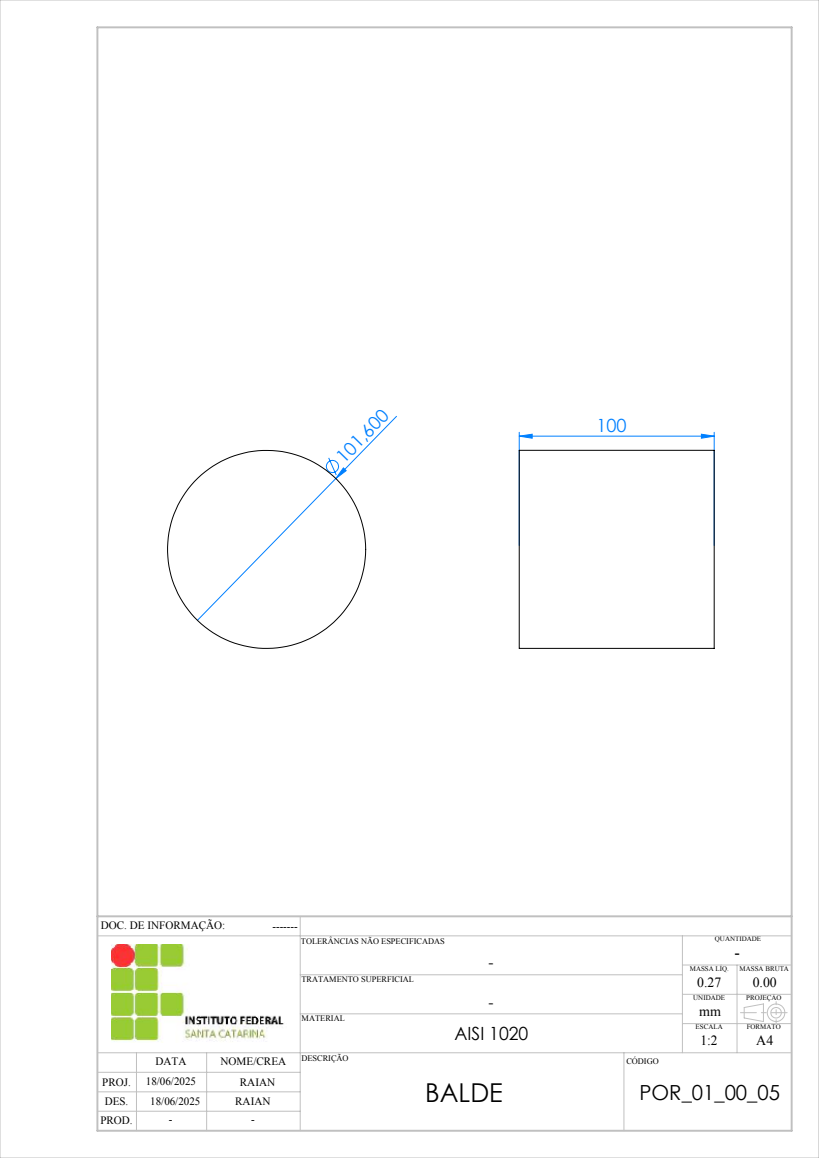
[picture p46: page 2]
BALDE; AISI 1020; DATA; NOME/CREA DESCRIÇÃO; CÓDIGO; MATERIAL; TRATAMENTO SUPERFICIAL; ESCALA; FORMATO; UNIDADE; MASSA LÍQ.; QUANTIDADE; RAIAN; POR_01_00_05 ¹⁸/06/2025; MASSA BRUTA 0.00; PROJEÇÃO

DOC. DE INFORMAÇÃO:

TOLERÂNCIAS NÃO ESPECIFICADAS

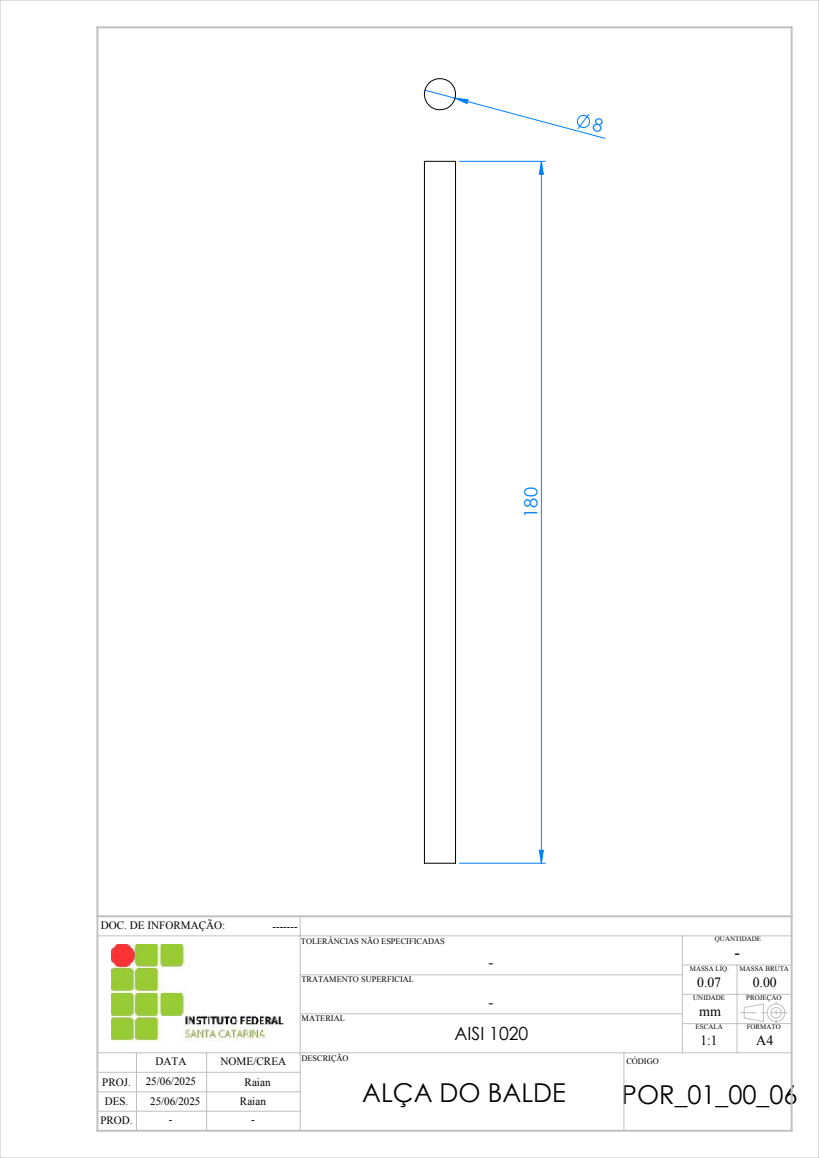
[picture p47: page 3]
ALÇA DO BALDE; AISI 1020; DATA; NOME/CREA DESCRIÇÃO; CÓDIGO; MATERIAL; TRATAMENTO SUPERFICIAL; ESCALA; FORMATO; UNIDADE; MASSA LÍQ.; QUANTIDADE; Raian; POR_01_00_06 ²⁵/06/2025; MASSA BRUTA 0.00; PROJEÇÃO

DOC. DE INFORMAÇÃO:

TOLERÂNCIAS NÃO ESPECIFICADAS

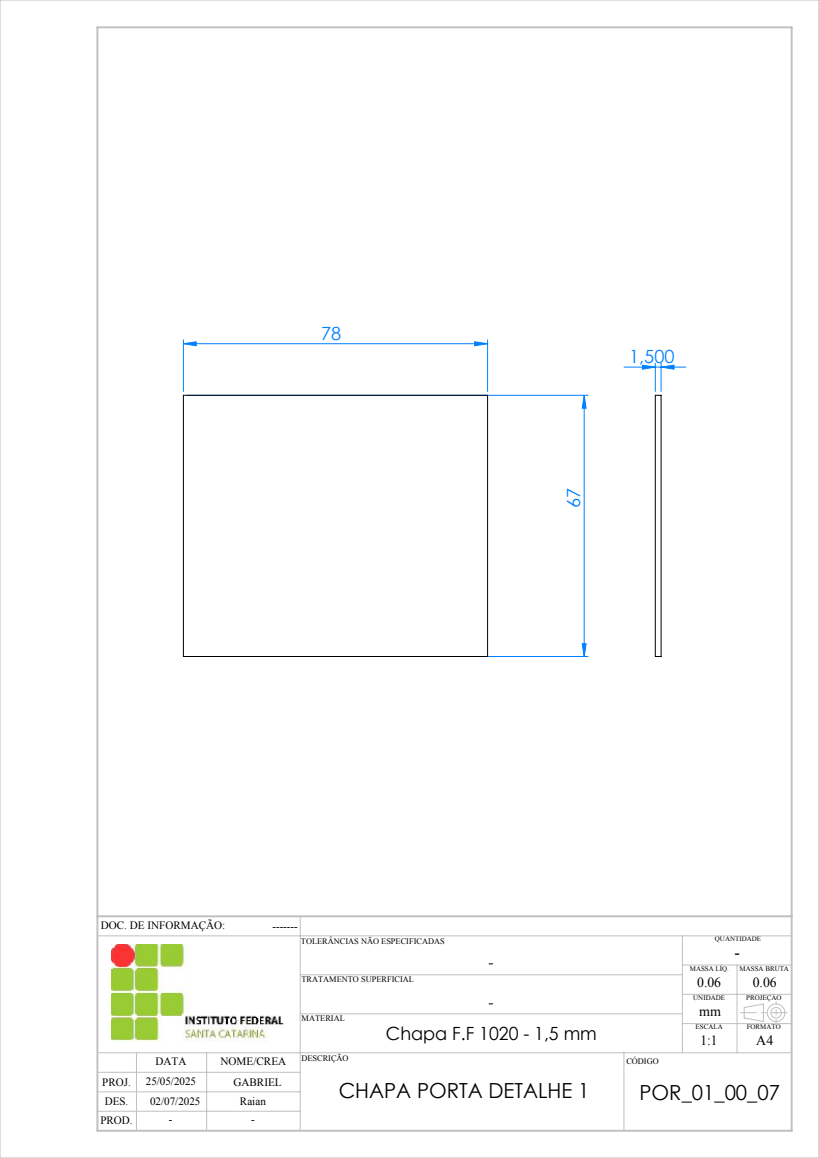
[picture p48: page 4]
Chapa F.F 1020 - 1,5 mm; DATA; NOME/CREA DESCRIÇÃO; CÓDIGO; MATERIAL; TRATAMENTO SUPERFICIAL; ESCALA; FORMATO; UNIDADE; MASSA LÍQ.; QUANTIDADE; GABRIEL; POR_01_00_07 ²⁵/05/2025; MASSA BRUTA 0.06; PROJEÇÃO; Raian

DOC. DE INFORMAÇÃO:

TOLERÂNCIAS NÃO ESPECIFICADAS

CHAPA PORTA DETALHE 1

131

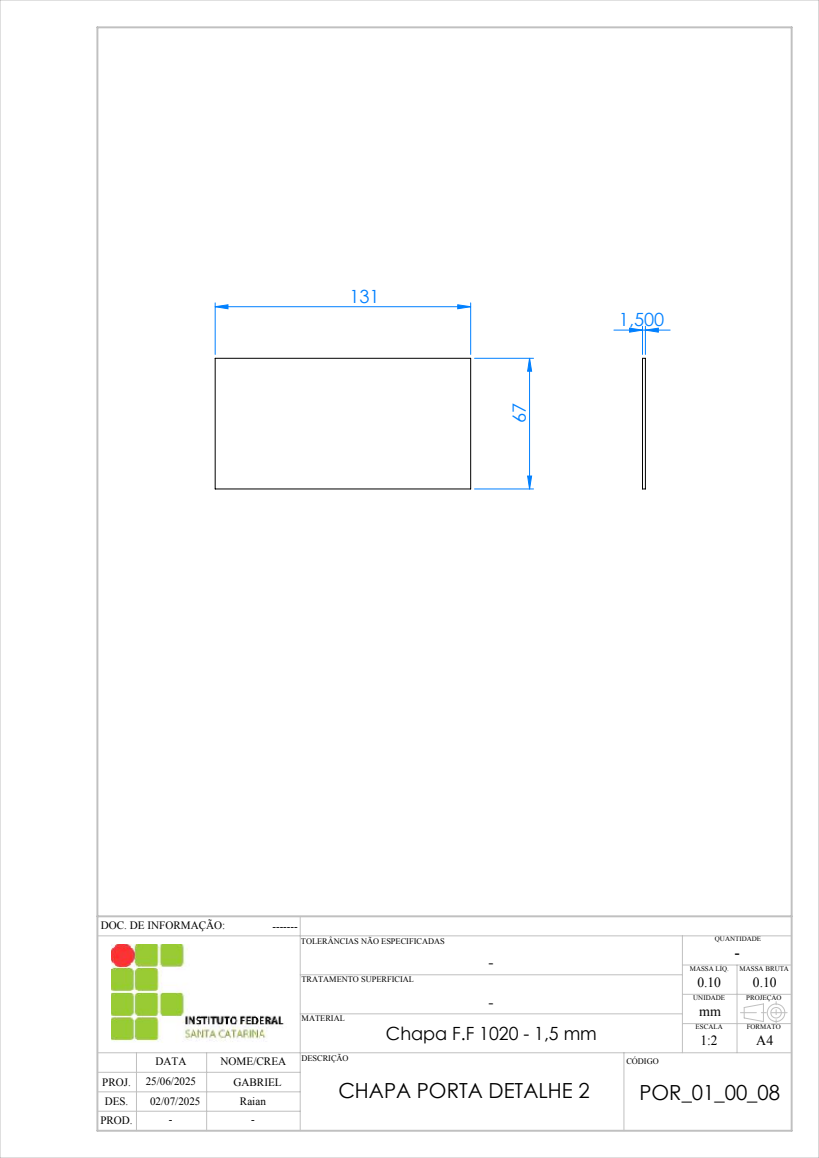
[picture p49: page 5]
Chapa F.F 1020 - 1,5 mm; DATA; NOME/CREA DESCRIÇÃO; CÓDIGO; MATERIAL; TRATAMENTO SUPERFICIAL; ESCALA; FORMATO; UNIDADE; MASSA LÍQ.; QUANTIDADE; POR_01_00_08 ²⁵/06/2025; MASSA BRUTA 0.10; PROJEÇÃO; Raian

DOC. DE INFORMAÇÃO:

TOLERÂNCIAS NÃO ESPECIFICADAS

CHAPA PORTA DETALHE 2

23
1,500

DOC. DE INFORMAÇÃO:

TOLERÂNCIAS NÃO ESPECIFICADAS

CHAPA PORTA DETALHE 3

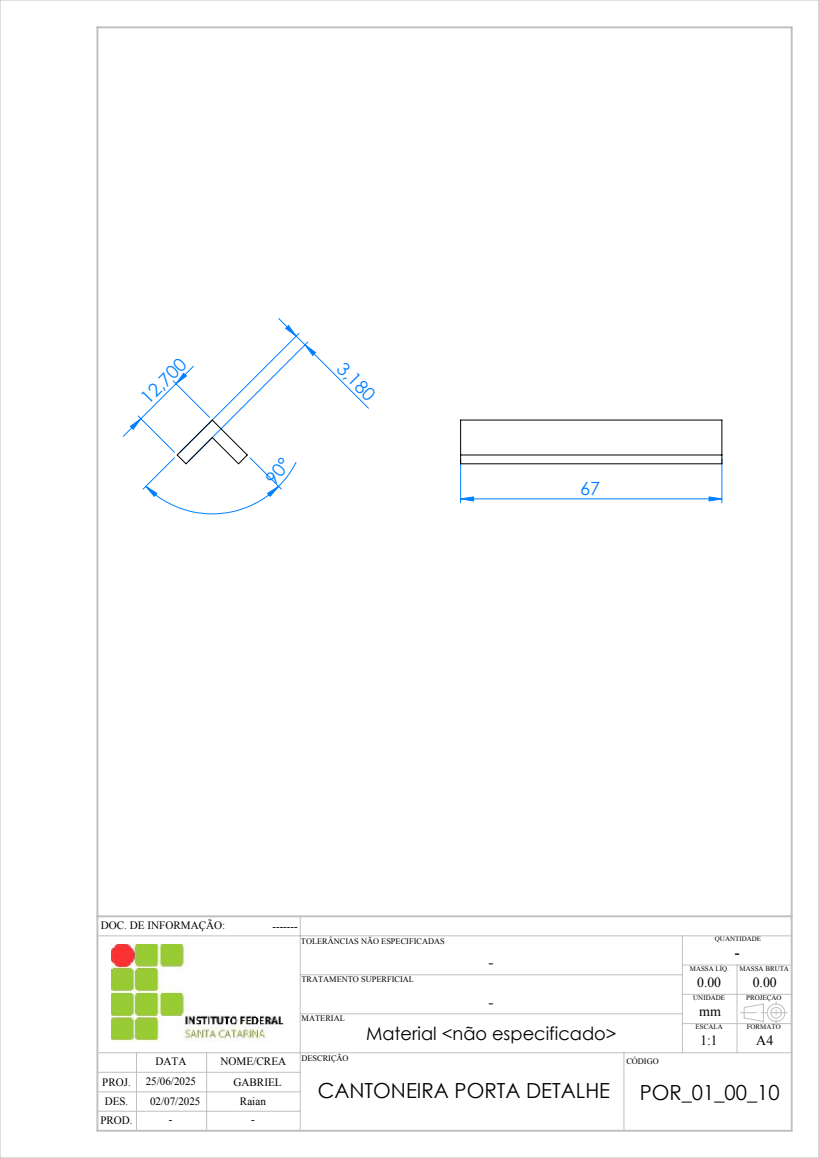
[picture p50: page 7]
DATA; NOME/CREA DESCRIÇÃO; CÓDIGO; TRATAMENTO SUPERFICIAL; ESCALA; FORMATO; UNIDADE; MASSA LÍQ.; QUANTIDADE; POR_01_00_10 ²⁵/06/2025; MASSA BRUTA 0.00; PROJEÇÃO; Raian

DOC. DE INFORMAÇÃO:

TOLERÂNCIAS NÃO ESPECIFICADAS

MATERIAL
Material <não especificado>

CANTONEIRA PORTA DETALHE

22

350

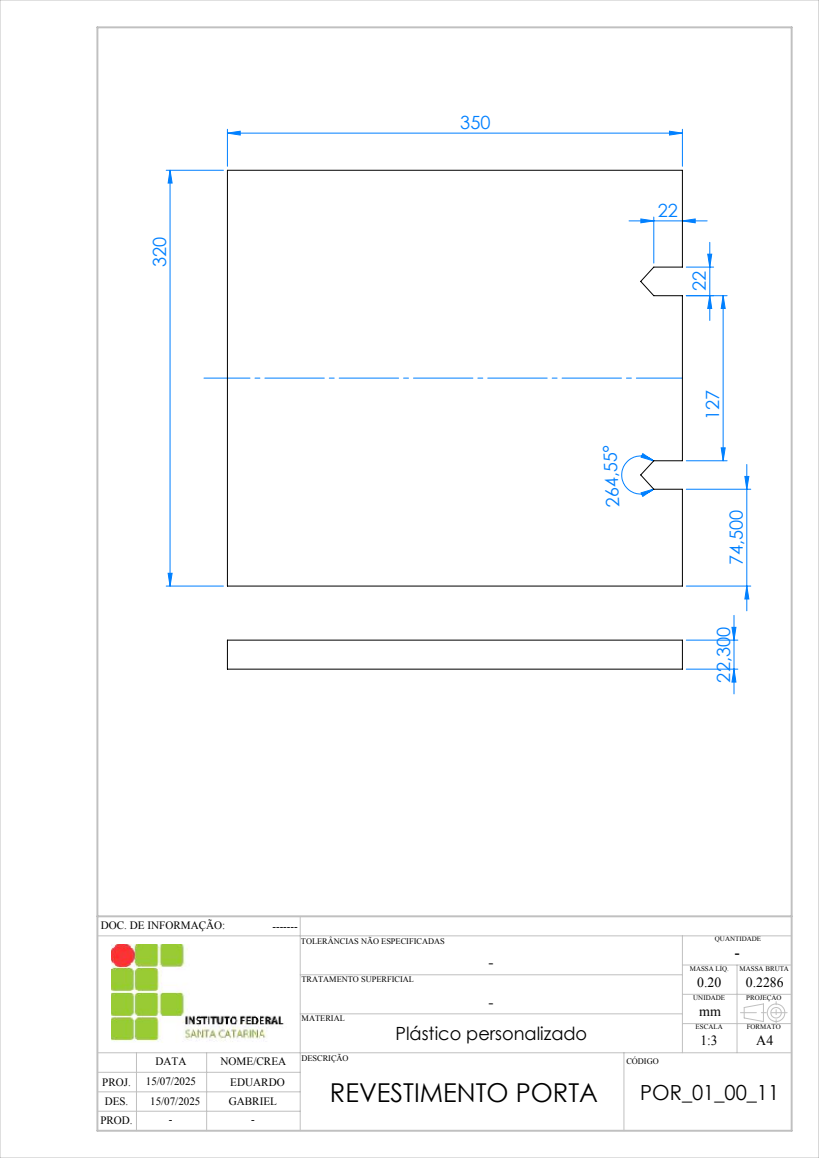
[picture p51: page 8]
REVESTIMENTO PORTA; Plástico personalizado; DATA; NOME/CREA DESCRIÇÃO; CÓDIGO; MATERIAL; TRATAMENTO SUPERFICIAL; ESCALA; FORMATO; UNIDADE; MASSA LÍQ.; QUANTIDADE; EDUARDO; POR_01_00_11 ¹⁵/07/2025; MASSA BRUTA 0.2286; PROJEÇÃO; GABRIEL

DOC. DE INFORMAÇÃO:

TOLERÂNCIAS NÃO ESPECIFICADAS

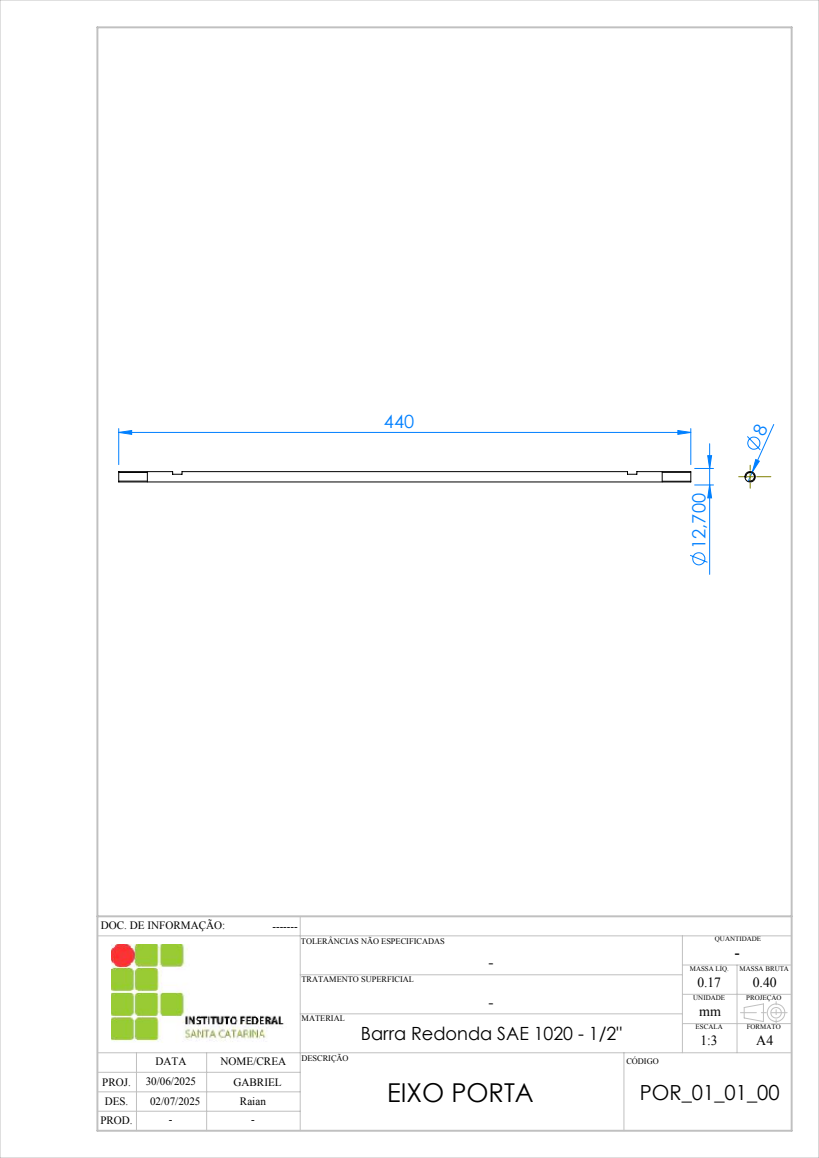
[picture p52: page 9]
DATA; NOME/CREA DESCRIÇÃO; CÓDIGO; TRATAMENTO SUPERFICIAL; ESCALA; FORMATO; UNIDADE; MASSA LÍQ.; QUANTIDADE; POR_01_01_00 ³⁰/06/2025; MASSA BRUTA 0.40; PROJEÇÃO; Raian

DOC. DE INFORMAÇÃO:

TOLERÂNCIAS NÃO ESPECIFICADAS

MATERIAL
Barra Redonda SAE 1020 - 1/2"
EIXO PORTA

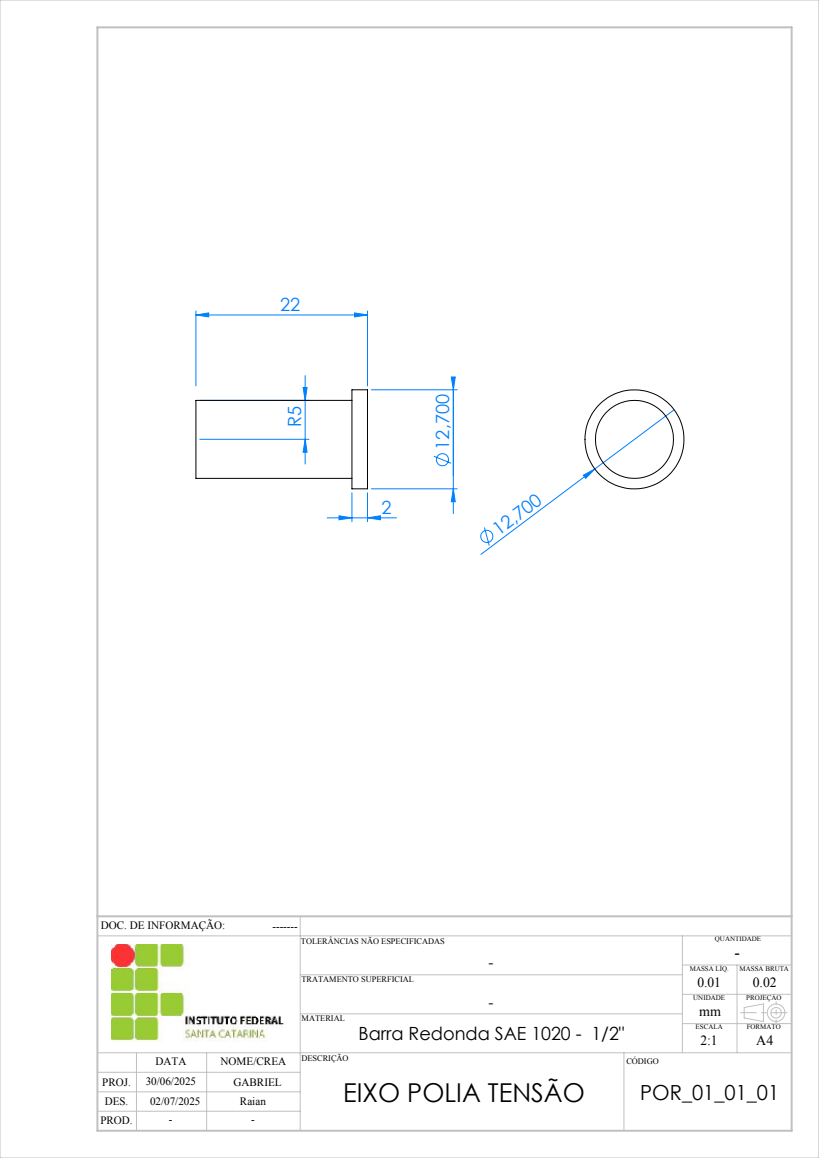
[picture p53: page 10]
DATA; NOME/CREA DESCRIÇÃO; CÓDIGO; TRATAMENTO SUPERFICIAL; ESCALA; FORMATO; UNIDADE; MASSA LÍQ.; QUANTIDADE; POR_01_01_01 ³⁰/06/2025; MASSA BRUTA 0.02; PROJEÇÃO; Raian

DOC. DE INFORMAÇÃO:

TOLERÂNCIAS NÃO ESPECIFICADAS

MATERIAL
Barra Redonda SAE 1020 - 1/2"
EIXO POLIA TENSÃO

300

2

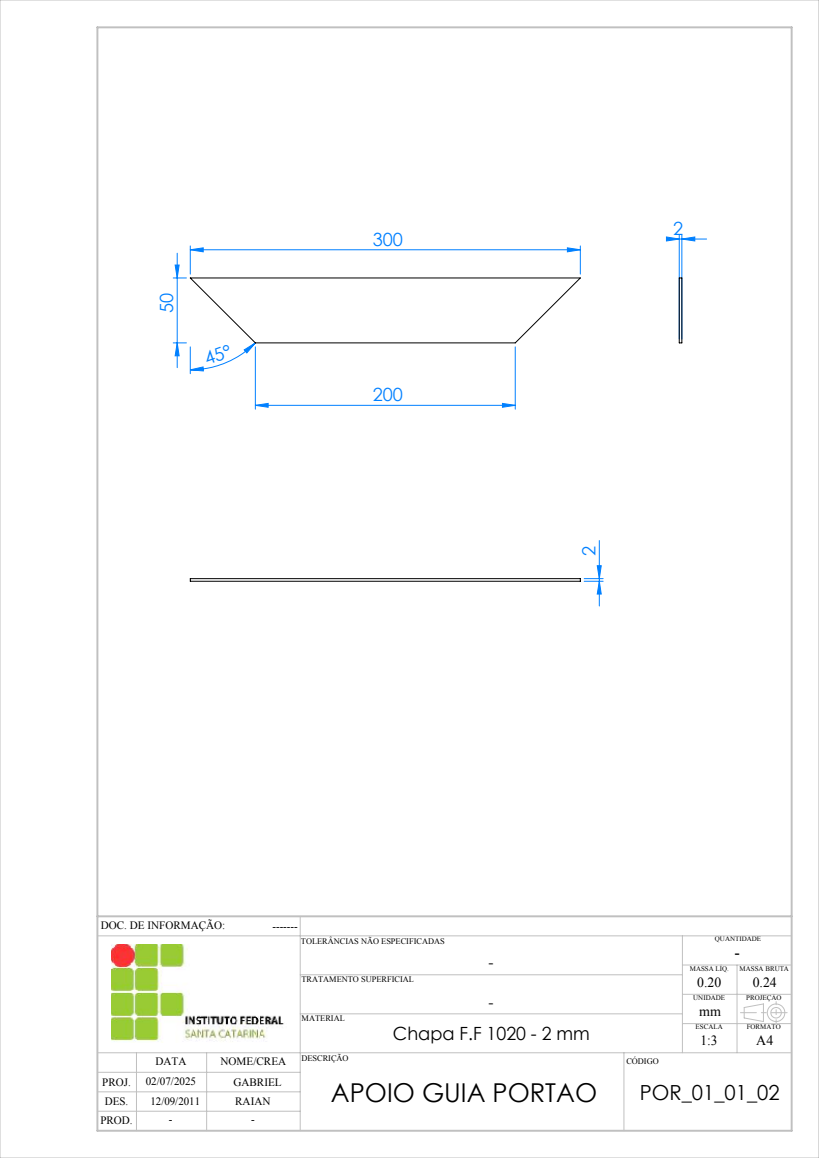
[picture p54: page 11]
Chapa F.F 1020 - 2 mm; DATA; NOME/CREA DESCRIÇÃO; CÓDIGO; TRATAMENTO SUPERFICIAL; ESCALA; FORMATO; UNIDADE; MASSA LÍQ.; QUANTIDADE; POR_01_01_02 ⁰²/07/2025; MASSA BRUTA 0.24; PROJEÇÃO; RAIAN

DOC. DE INFORMAÇÃO:

TOLERÂNCIAS NÃO ESPECIFICADAS

MATERIAL
APOIO GUIA PORTAO

90
25

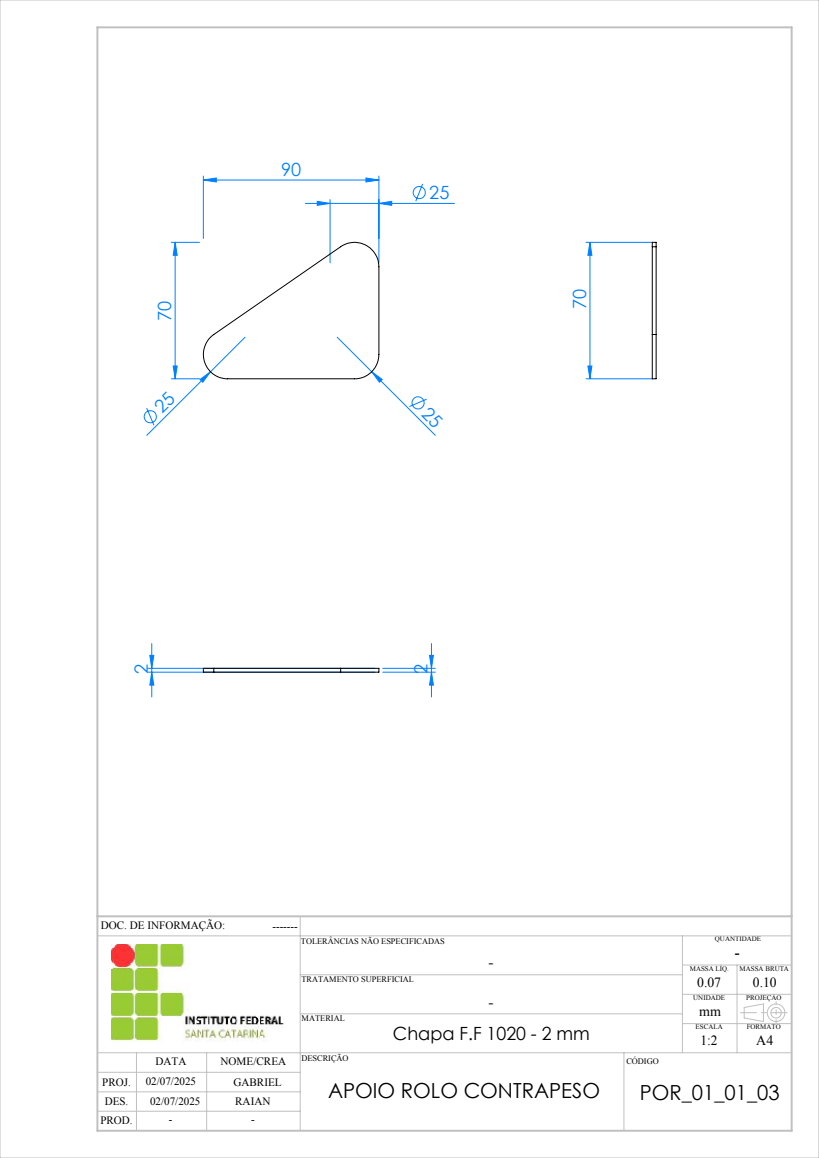
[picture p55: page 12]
Chapa F.F 1020 - 2 mm; DATA; NOME/CREA DESCRIÇÃO; CÓDIGO; MATERIAL; TRATAMENTO SUPERFICIAL; ESCALA; FORMATO; UNIDADE; MASSA LÍQ.; QUANTIDADE; POR_01_01_03 ⁰²/07/2025; MASSA BRUTA 0.10; PROJEÇÃO; RAIAN

DOC. DE INFORMAÇÃO:

TOLERÂNCIAS NÃO ESPECIFICADAS

APOIO ROLO CONTRAPESO

36,5

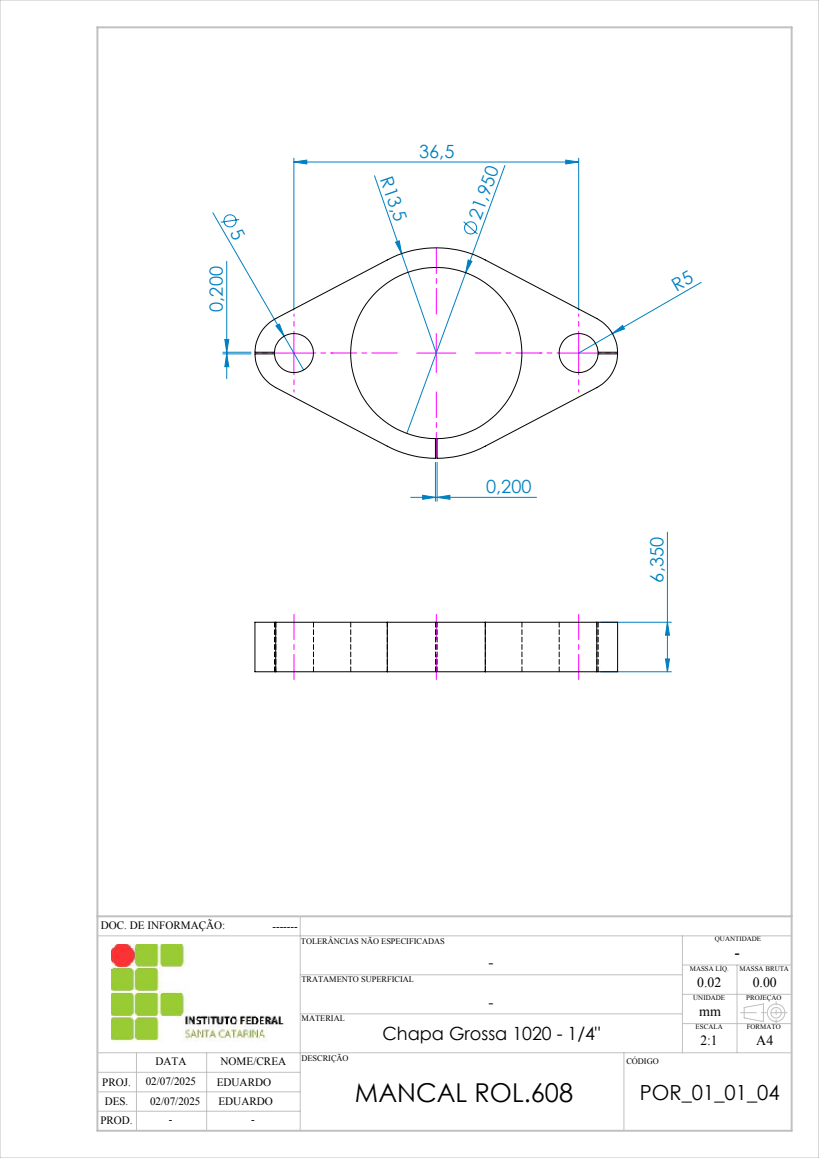
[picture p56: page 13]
MANCAL ROL.608; Chapa Grossa 1020 - 1/4"; DATA; NOME/CREA DESCRIÇÃO; CÓDIGO; MATERIAL; TRATAMENTO SUPERFICIAL; ESCALA; FORMATO; UNIDADE; MASSA LÍQ.; QUANTIDADE; EDUARDO; POR_01_01_04 ⁰²/07/2025; MASSA BRUTA 0.00; PROJEÇÃO

DOC. DE INFORMAÇÃO:

TOLERÂNCIAS NÃO ESPECIFICADAS

9

4

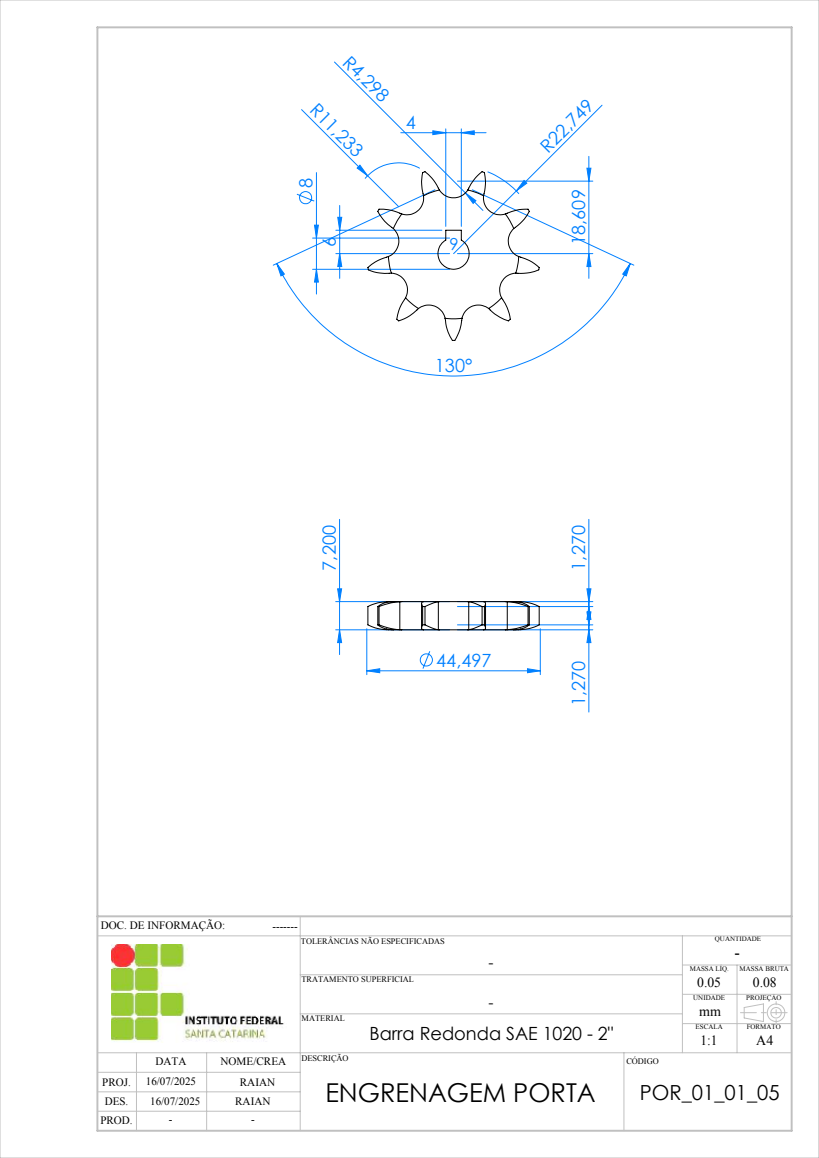
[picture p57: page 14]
DATA; NOME/CREA DESCRIÇÃO; CÓDIGO; TRATAMENTO SUPERFICIAL; ESCALA; FORMATO; UNIDADE; MASSA LÍQ.; QUANTIDADE; RAIAN; POR_01_01_05 ¹⁶/07/2025; MASSA BRUTA 0.08; PROJEÇÃO

DOC. DE INFORMAÇÃO:

TOLERÂNCIAS NÃO ESPECIFICADAS

MATERIAL
Barra Redonda SAE 1020 - 2"
ENGRENAGEM PORTA

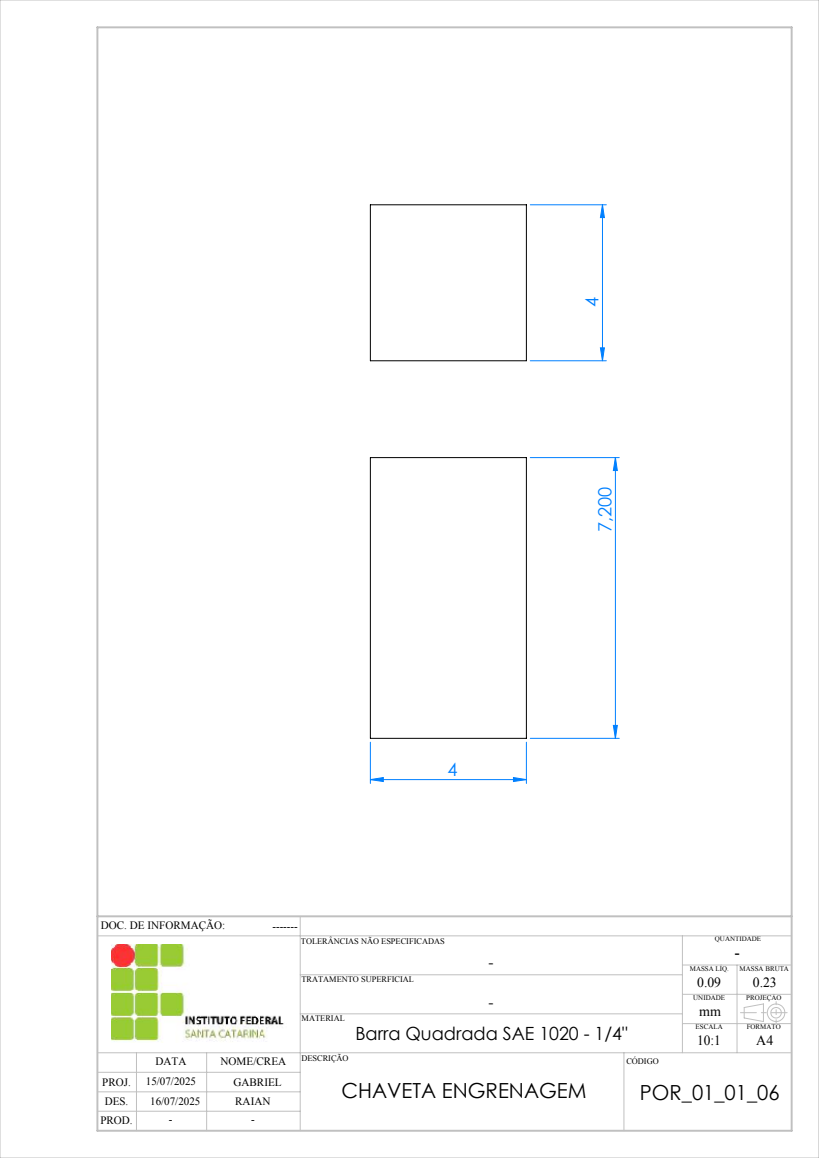
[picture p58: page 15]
CHAVETA ENGRENAGEM; DATA; NOME/CREA DESCRIÇÃO; CÓDIGO; TRATAMENTO SUPERFICIAL; ESCALA; FORMATO; UNIDADE; MASSA LÍQ.; QUANTIDADE; POR_01_01_06 ¹⁵/07/2025; MASSA BRUTA 0.23; PROJEÇÃO

DOC. DE INFORMAÇÃO:

TOLERÂNCIAS NÃO ESPECIFICADAS

MATERIAL
Barra Quadrada SAE 1020 - 1/4"

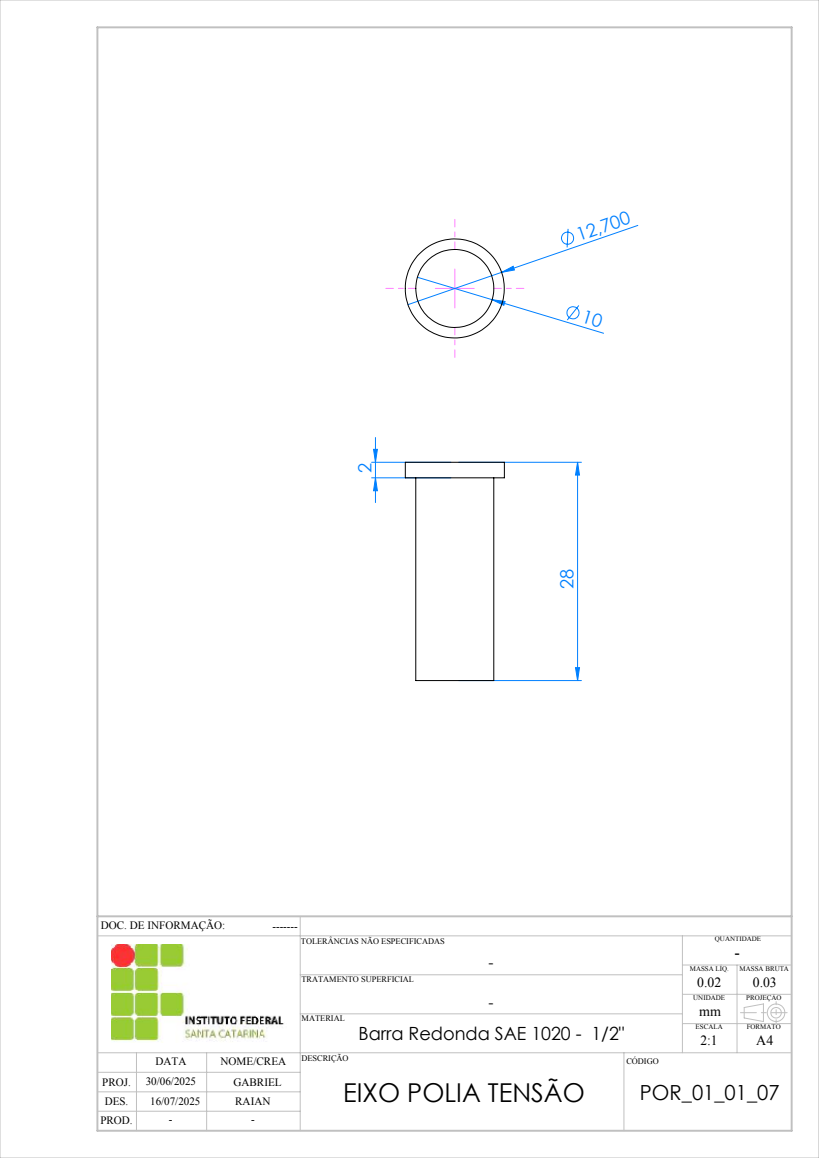
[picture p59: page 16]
DATA; NOME/CREA DESCRIÇÃO; CÓDIGO; TRATAMENTO SUPERFICIAL; ESCALA; FORMATO; UNIDADE; MASSA LÍQ.; QUANTIDADE; POR_01_01_07 ³⁰/06/2025; MASSA BRUTA 0.03; PROJEÇÃO

DOC. DE INFORMAÇÃO:

TOLERÂNCIAS NÃO ESPECIFICADAS

MATERIAL
Barra Redonda SAE 1020 - 1/2"
EIXO POLIA TENSÃO

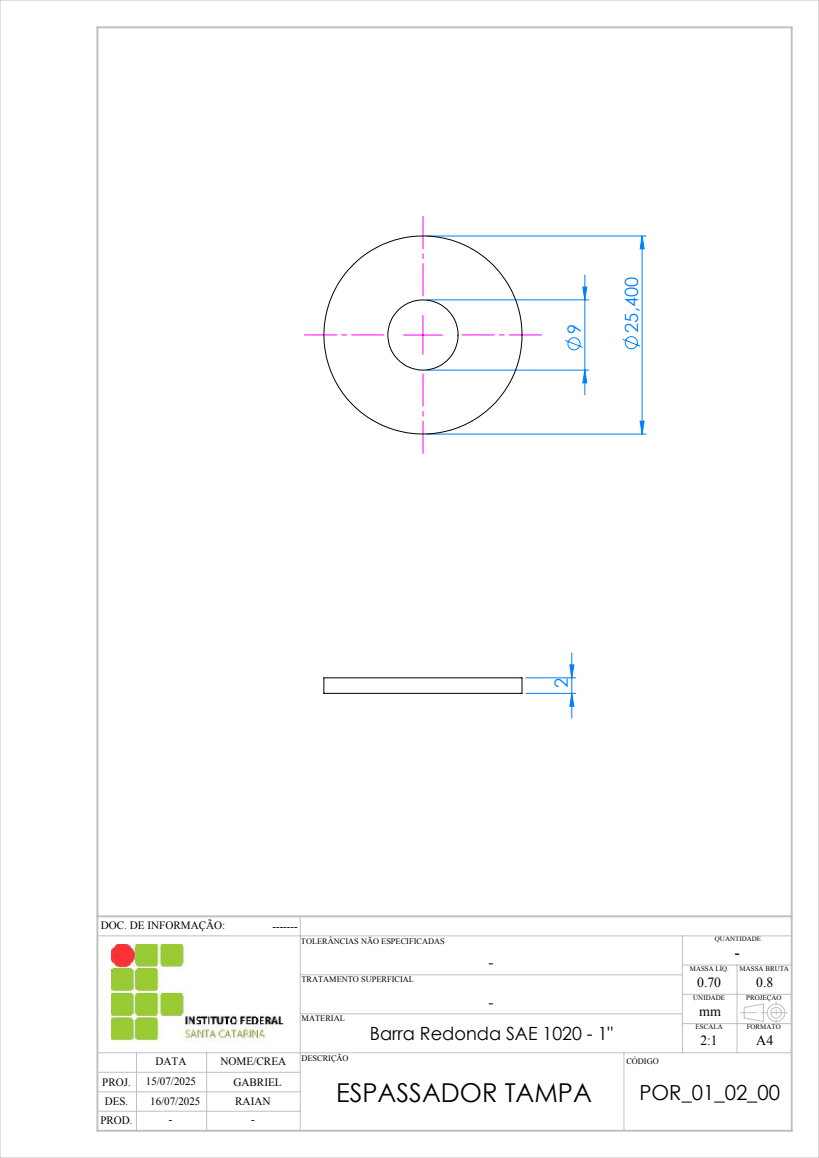
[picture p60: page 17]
DATA; NOME/CREA DESCRIÇÃO; CÓDIGO; TRATAMENTO SUPERFICIAL; ESCALA; FORMATO; UNIDADE; MASSA LÍQ.; QUANTIDADE; POR_01_02_00 ¹⁵/07/2025; MASSA BRUTA 0.8; PROJEÇÃO

DOC. DE INFORMAÇÃO:

TOLERÂNCIAS NÃO ESPECIFICADAS

MATERIAL
Barra Redonda SAE 1020 - 1"
ESPASSADOR TAMPA

DOC. DE INFORMAÇÃO:

TOLERÂNCIAS NÃO ESPECIFICADAS

MATERIAL
Tubo redondo com costura - 1/2" x 1,2

ESPAÇADOR CORPO MEDIO

1,200

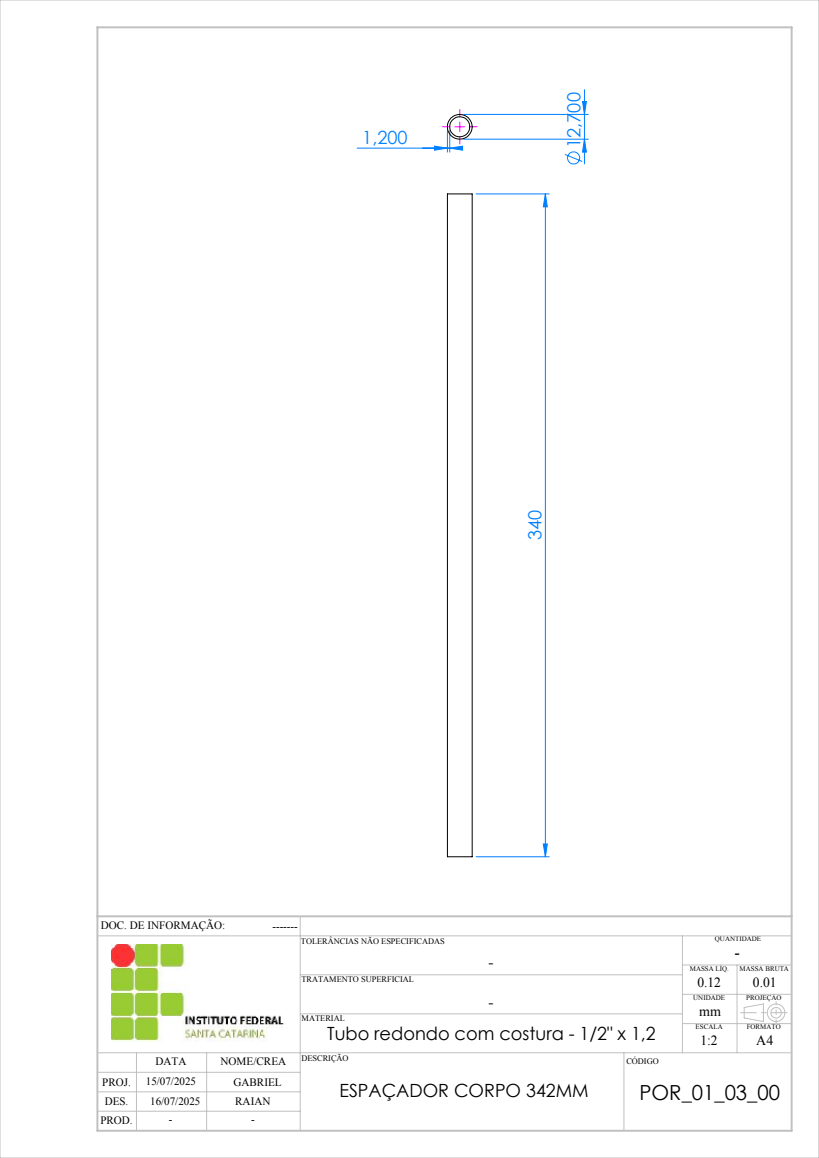
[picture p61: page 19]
ESPAÇADOR CORPO 342MM; DATA; NOME/CREA DESCRIÇÃO; CÓDIGO; TRATAMENTO SUPERFICIAL; ESCALA; FORMATO; UNIDADE; MASSA LÍQ.; QUANTIDADE; POR_01_03_00 ¹⁵/07/2025; MASSA BRUTA 0.01; PROJEÇÃO

DOC. DE INFORMAÇÃO:

TOLERÂNCIAS NÃO ESPECIFICADAS

MATERIAL
Tubo redondo com costura - 1/2" x 1,2

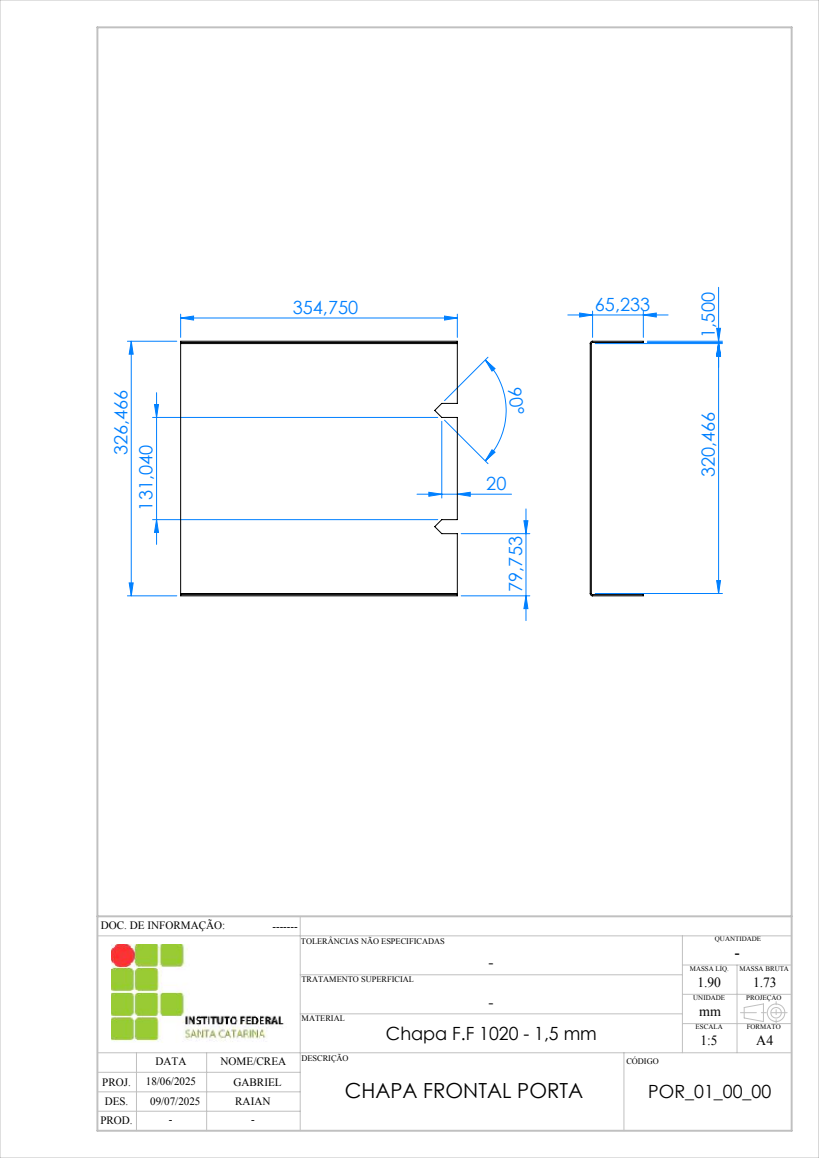
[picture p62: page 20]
Chapa F.F 1020 - 1,5 mm; DATA; NOME/CREA DESCRIÇÃO; CÓDIGO; MATERIAL; TRATAMENTO SUPERFICIAL; ESCALA; FORMATO; UNIDADE; MASSA LÍQ.; QUANTIDADE; POR_01_00_00 ¹⁸/06/2025; MASSA BRUTA 1.73; PROJEÇÃO

DOC. DE INFORMAÇÃO:

TOLERÂNCIAS NÃO ESPECIFICADAS

CHAPA FRONTAL PORTA

67
1,500

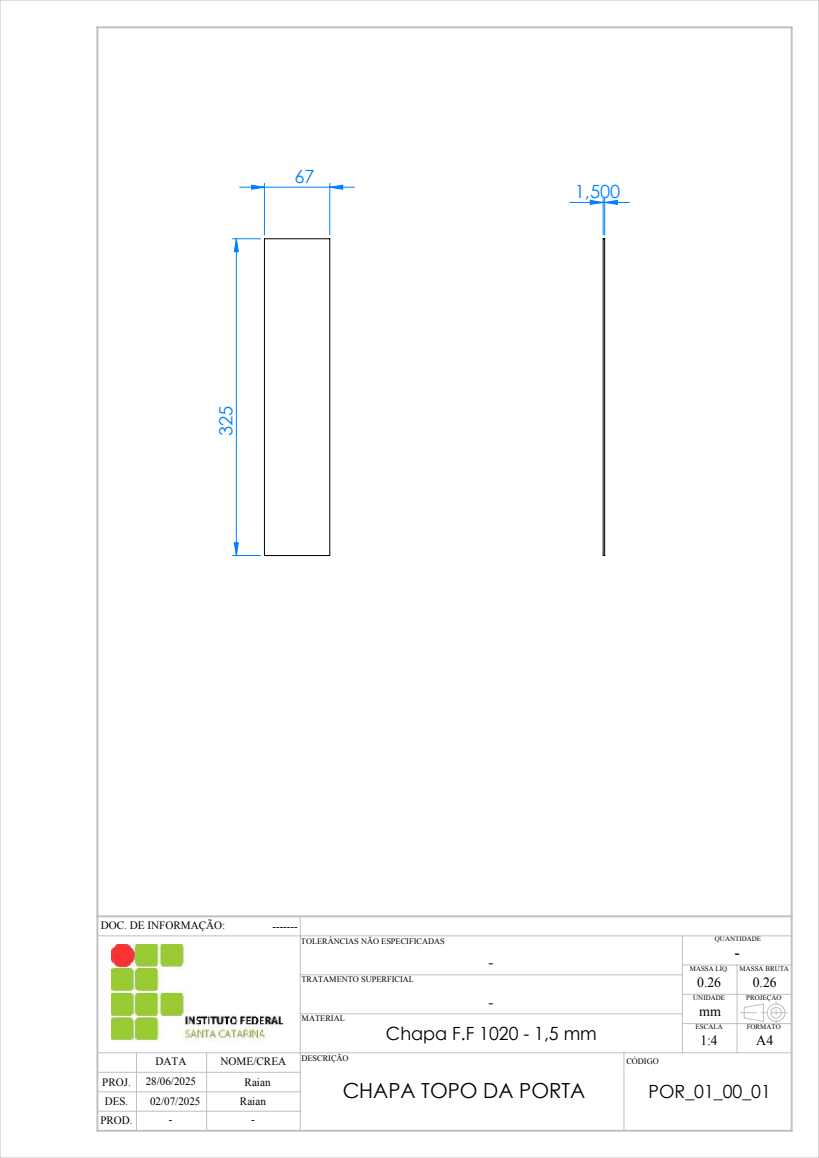
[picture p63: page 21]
Chapa F.F 1020 - 1,5 mm; DATA; NOME/CREA DESCRIÇÃO; CÓDIGO; MATERIAL; TRATAMENTO SUPERFICIAL; ESCALA; FORMATO; UNIDADE; MASSA LÍQ.; QUANTIDADE; Raian; POR_01_00_01 ²⁸/06/2025; MASSA BRUTA 0.26; PROJEÇÃO

DOC. DE INFORMAÇÃO:

TOLERÂNCIAS NÃO ESPECIFICADAS

CHAPA TOPO DA PORTA

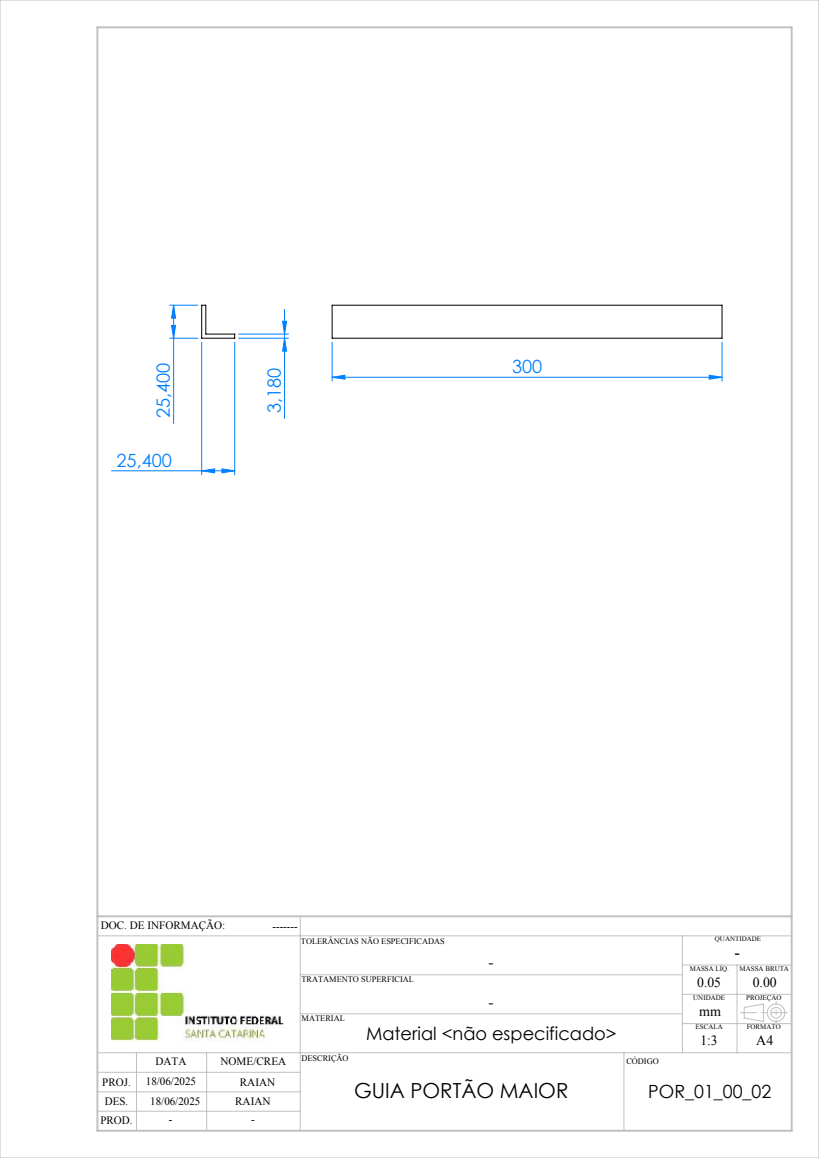
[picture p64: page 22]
DATA; NOME/CREA DESCRIÇÃO; CÓDIGO; TRATAMENTO SUPERFICIAL; ESCALA; FORMATO; UNIDADE; MASSA LÍQ.; QUANTIDADE; RAIAN; POR_01_00_02 ¹⁸/06/2025; MASSA BRUTA 0.00; PROJEÇÃO

DOC. DE INFORMAÇÃO:

TOLERÂNCIAS NÃO ESPECIFICADAS

MATERIAL
Material <não especificado>

GUIA PORTÃO MAIOR

2,500

30

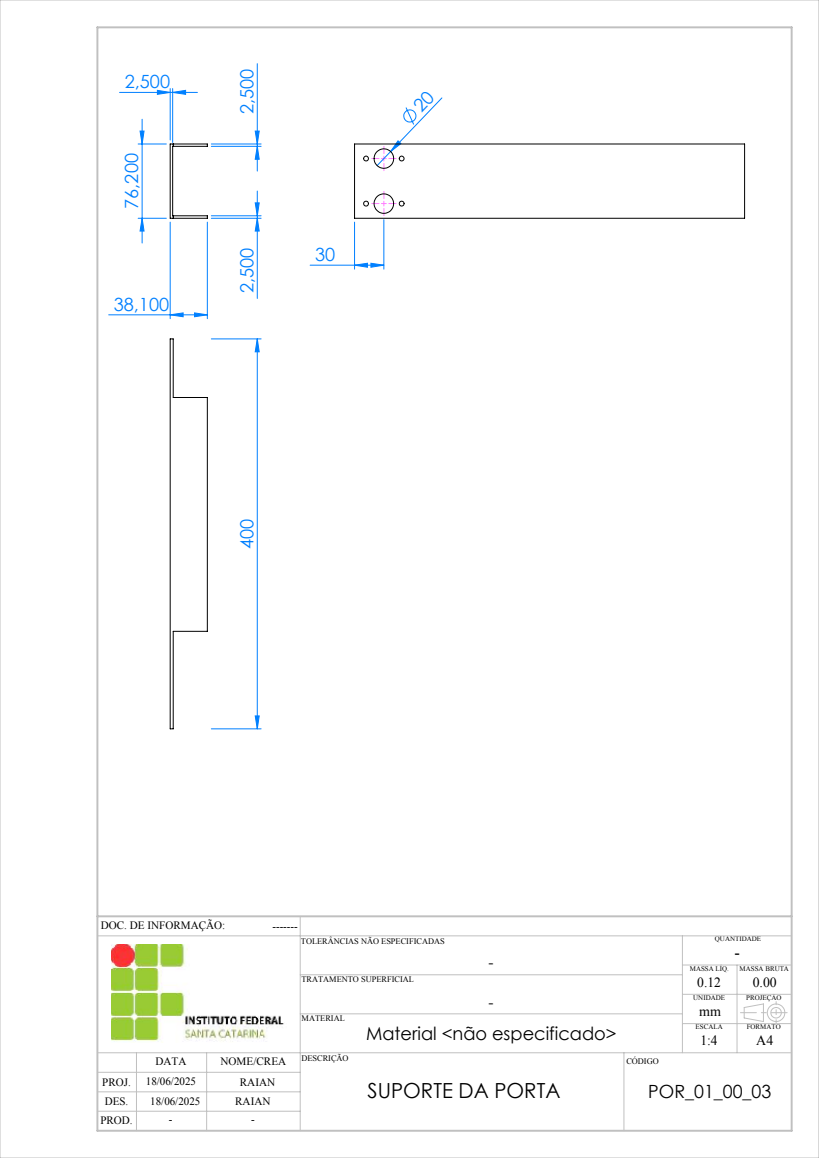
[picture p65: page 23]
DATA; NOME/CREA DESCRIÇÃO; CÓDIGO; TRATAMENTO SUPERFICIAL; ESCALA; FORMATO; UNIDADE; MASSA LÍQ.; QUANTIDADE; RAIAN; POR_01_00_03 ¹⁸/06/2025; MASSA BRUTA 0.00; PROJEÇÃO

DOC. DE INFORMAÇÃO:

TOLERÂNCIAS NÃO ESPECIFICADAS

MATERIAL
Material <não especificado>

SUPORTE DA PORTA

8

6

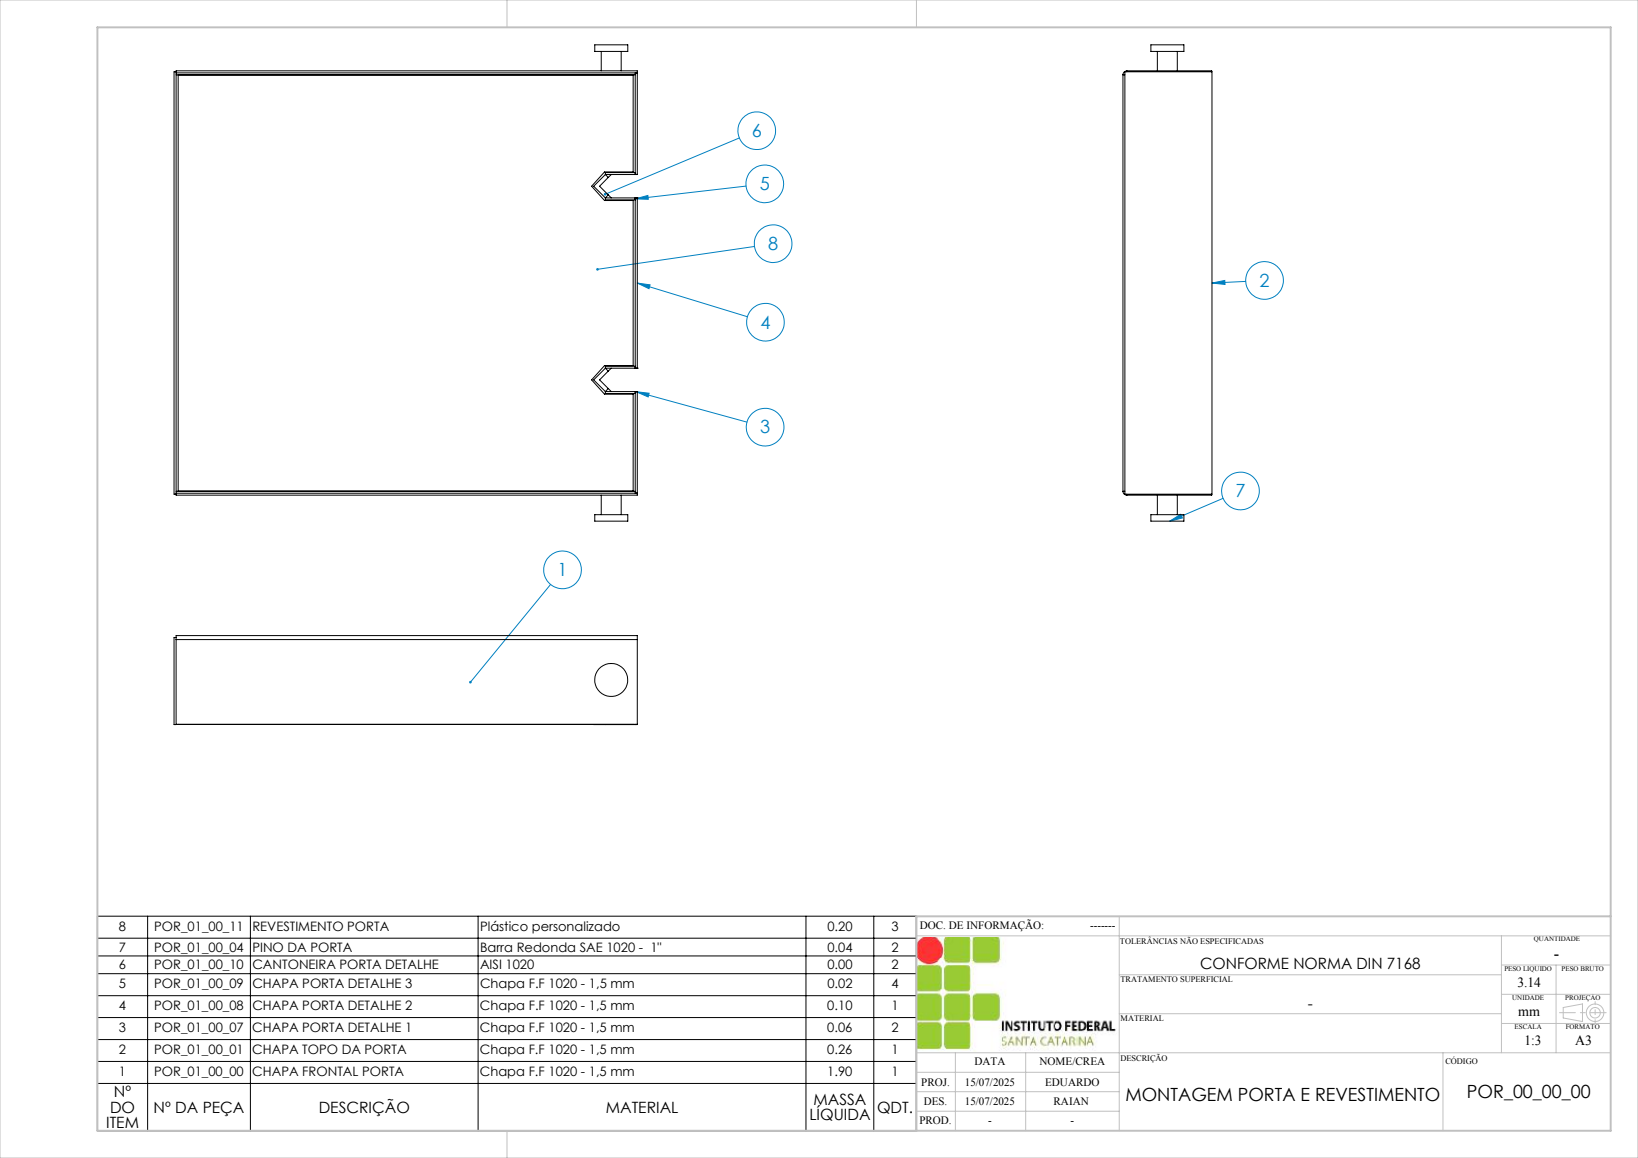
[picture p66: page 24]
MATERIAL

8 | POR_01_00_11 | REVESTIMENTO PORTA | Plástico personalizado | 0.20 | 3 | DOC. DE INFORMAÇÃO: -------QUANTIDADE TOLERÂNCIAS NÃO ESPECIFICADAS CONFORME NORMA DIN 7168 -PESO LIQUIDO PESO BRUTO TRATAMENTO SUPERFICIAL 3.14 UNIDADE PROJEÇÃO ESCALA FORMATO 1:3 A3 DATA NOME/CREA DESCRIÇÃO CÓDIGO 15/07/2025 EDUARDO MONTAGEM PORTA E REVESTIMENTO POR_00_00_00 PROJ. --
7 | POR_01_00_04 | PINO DA PORTA | Barra Redonda SAE 1020 - 1" | 0.04 | 2
6 | POR_01_00_10 | CANTONEIRA PORTA DETALHE | AISI 1020 | 0.00 | 2
5 | POR_01_00_09 | CHAPA PORTA DETALHE 3 | Chapa F.F 1020 - 1,5 mm | 0.02 | 4
4 | POR_01_00_08 | CHAPA PORTA DETALHE 2 | Chapa F.F 1020 - 1,5 mm | 0.10 | 1
3 | POR_01_00_07 | CHAPA PORTA DETALHE 1 | Chapa F.F 1020 - 1,5 mm | 0.06 | 2
2 | POR_01_00_01 | CHAPA TOPO DA PORTA | Chapa F.F 1020 - 1,5 mm | 0.26 | 1
1 | POR_01_00_00 | CHAPA FRONTAL PORTA | Chapa F.F 1020 - 1,5 mm | 1.90 | 1
Nº DO ITEM | Nº DA PEÇA | DESCRIÇÃO | MATERIAL | LÍQUIDA MASSA | QDT.

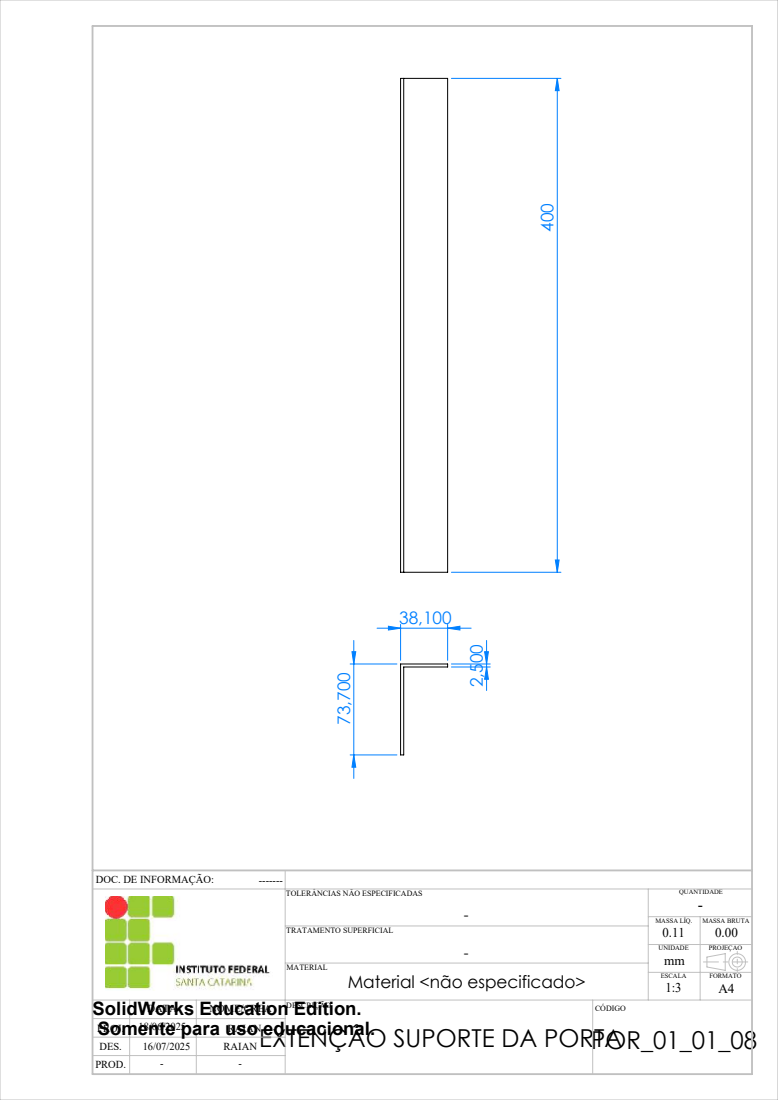
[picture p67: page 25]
DATA; NOME/CREA DESCRIÇÃO; CÓDIGO; TRATAMENTO SUPERFICIAL; ESCALA; FORMATO; UNIDADE; MASSA LÍQ.; QUANTIDADE; RAIAN; MASSA BRUTA 0.00; PROJEÇÃO

DOC. DE INFORMAÇÃO:

TOLERÂNCIAS NÃO ESPECIFICADAS

MATERIAL
Material <não especificado>
EXTENÇÂO SUPORTE DA PORTA

SolidWorks Education Edition.
Somente para uso educacional.
POR_01_01_08 ¹⁸/06/2025

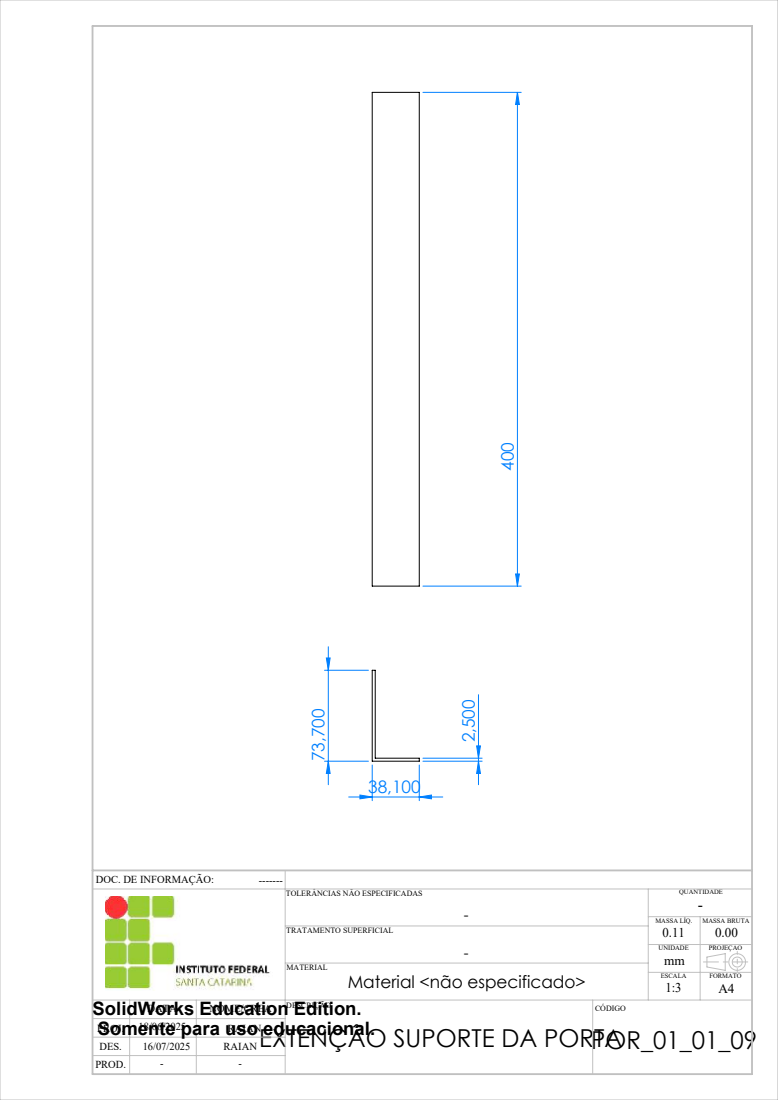
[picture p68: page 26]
DATA; NOME/CREA DESCRIÇÃO; CÓDIGO; TRATAMENTO SUPERFICIAL; ESCALA; FORMATO; UNIDADE; MASSA LÍQ.; QUANTIDADE; RAIAN; MASSA BRUTA 0.00; PROJEÇÃO

DOC. DE INFORMAÇÃO:

TOLERÂNCIAS NÃO ESPECIFICADAS

MATERIAL
Material <não especificado>
EXTENÇÂO SUPORTE DA PORTA

SolidWorks Education Edition.
Somente para uso educacional.
POR_01_01_09 ¹⁸/06/2025

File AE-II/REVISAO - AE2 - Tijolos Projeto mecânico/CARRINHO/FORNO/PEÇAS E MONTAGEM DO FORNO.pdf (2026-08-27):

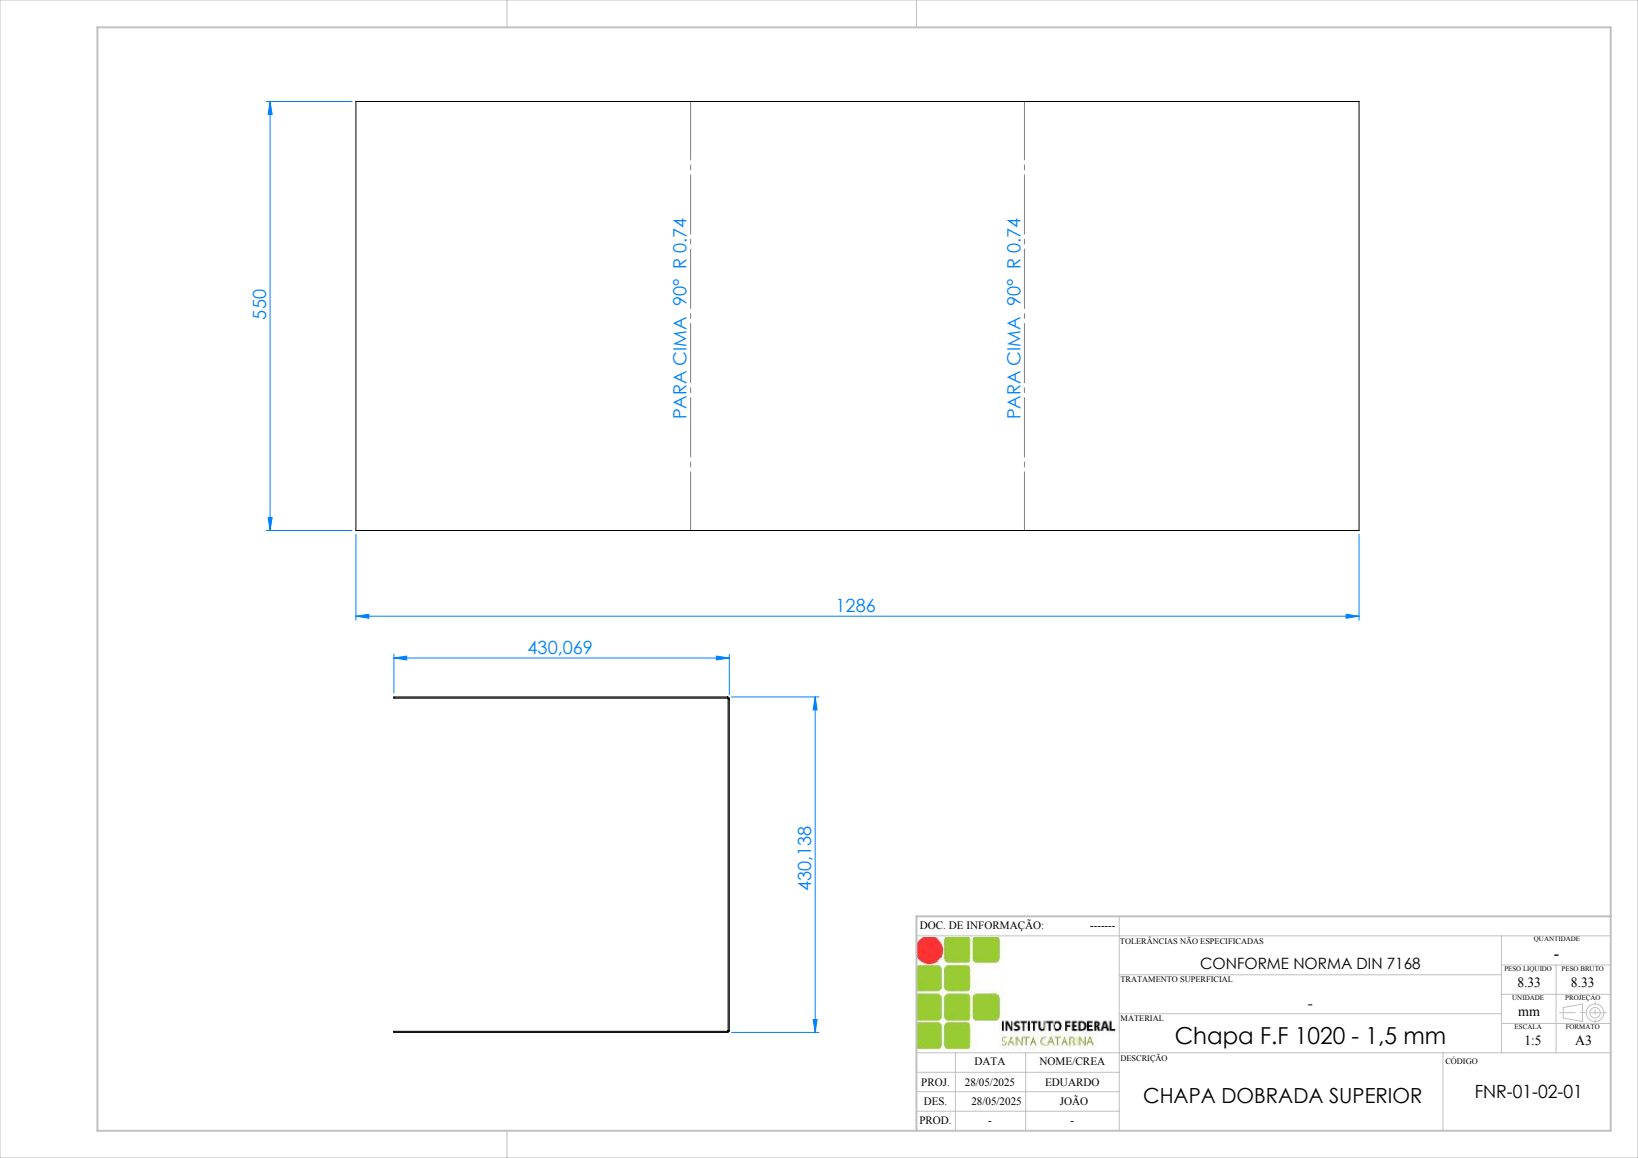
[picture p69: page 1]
PARA CIMA 90° R 0.74; CHAPA DOBRADA SUPERIOR; FNR-01-02-01; Chapa F.F 1020 - 1,5 mm; PROJ. DES. PROD.; DATA; NOME/CREA DESCRIÇÃO; CÓDIGO; MATERIAL; TRATAMENTO SUPERFICIAL; ESCALA; FORMATO; UNIDADE; PROJEÇÃO; QUANTIDADE; DOC. DE INFORMAÇÃO:; EDUARDO; JOÃO; CONFORME NORMA DIN 7168

TOLERÂNCIAS NÃO ESPECIFICADAS

PESO LIQUIDO PESO BRUTO

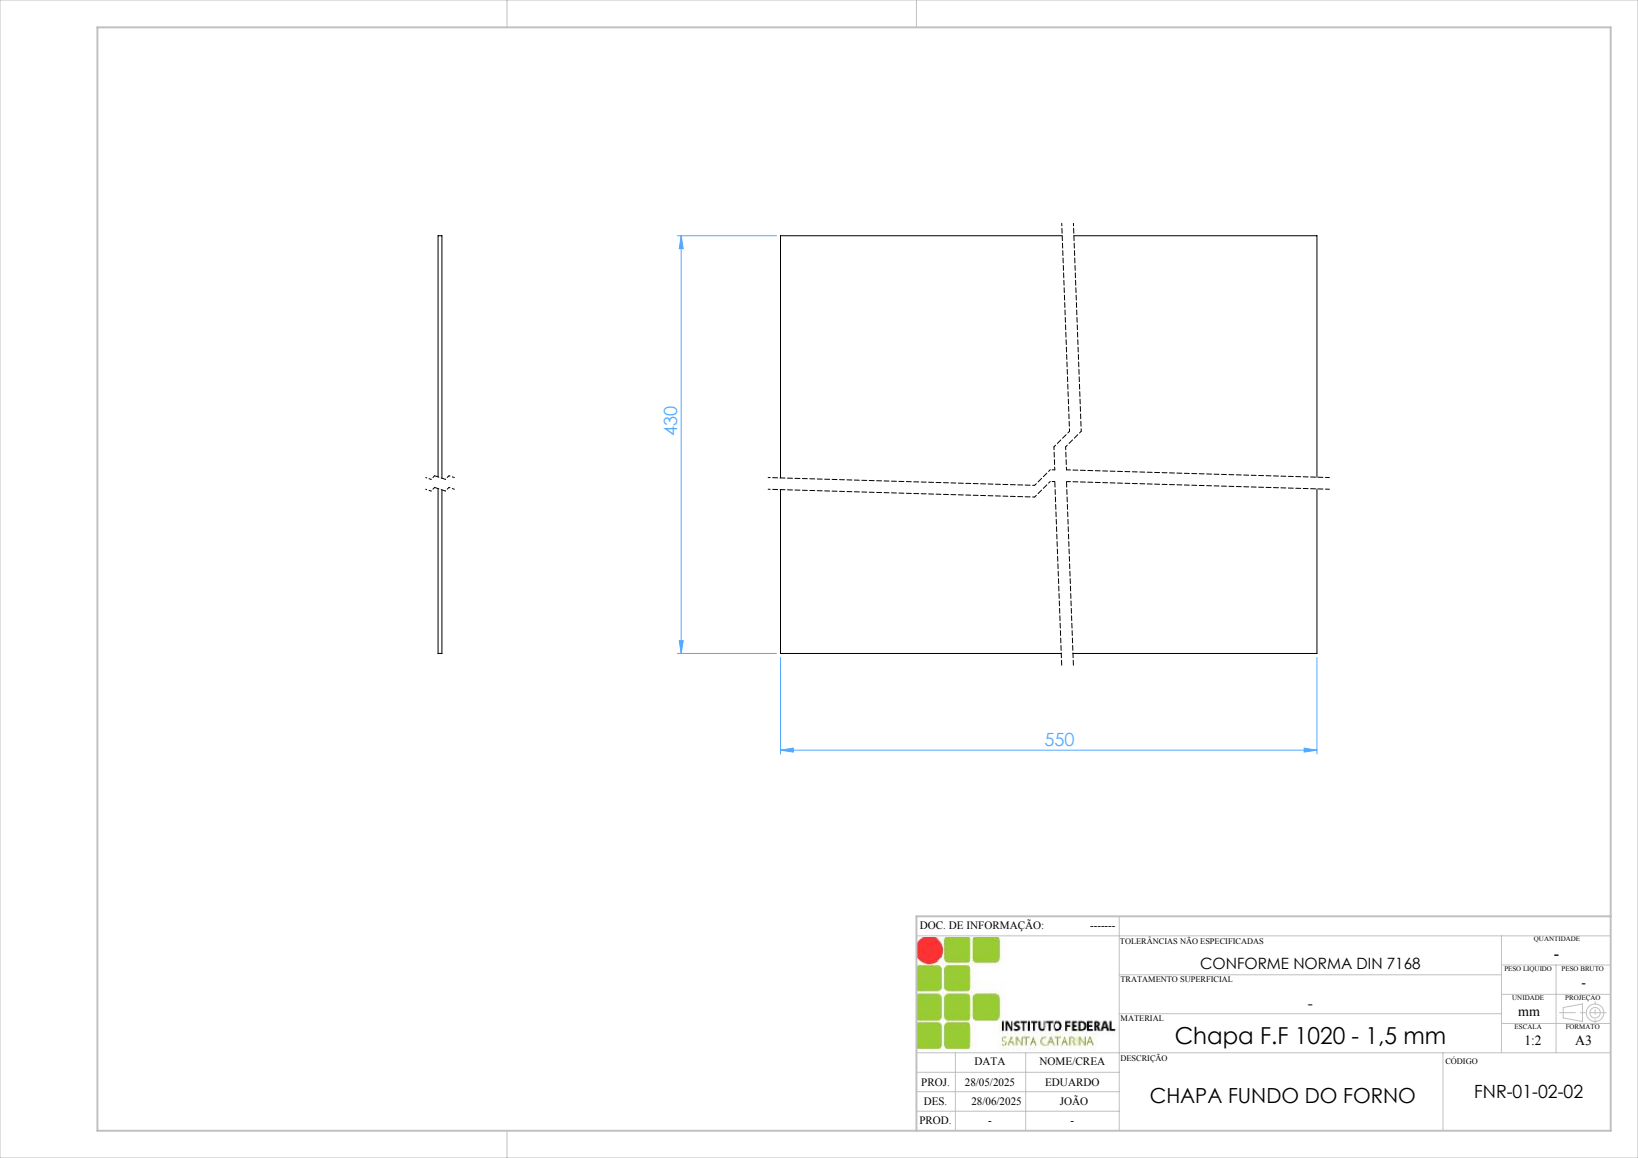
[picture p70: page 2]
- CHAPA FUNDO DO FORNO; FNR-01-02-02; Chapa F.F 1020 - 1,5 mm; DATA; NOME/CREA DESCRIÇÃO; CÓDIGO; MATERIAL; TRATAMENTO SUPERFICIAL; ESCALA; FORMATO; UNIDADE; PROJEÇÃO; QUANTIDADE; DOC. DE INFORMAÇÃO:; JOÃO; CONFORME NORMA DIN 7168

TOLERÂNCIAS NÃO ESPECIFICADAS

PESO LIQUIDO PESO BRUTO

50

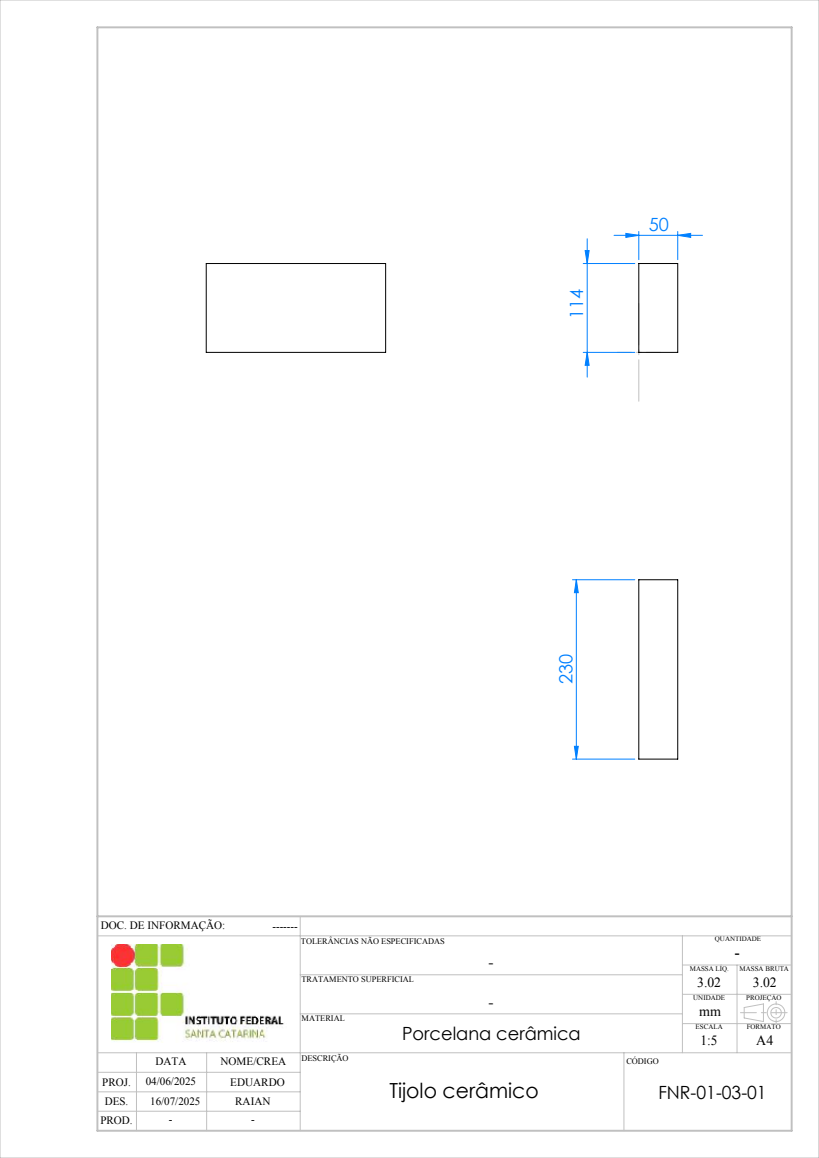
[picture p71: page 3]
Tijolo cerâmico; Porcelana cerâmica; DATA; NOME/CREA DESCRIÇÃO; CÓDIGO; MATERIAL; TRATAMENTO SUPERFICIAL; ESCALA; FORMATO; UNIDADE; MASSA LÍQ.; QUANTIDADE; FNR-01-03-01; MASSA BRUTA 3.02; PROJEÇÃO; RAIAN

DOC. DE INFORMAÇÃO:

TOLERÂNCIAS NÃO ESPECIFICADAS

420

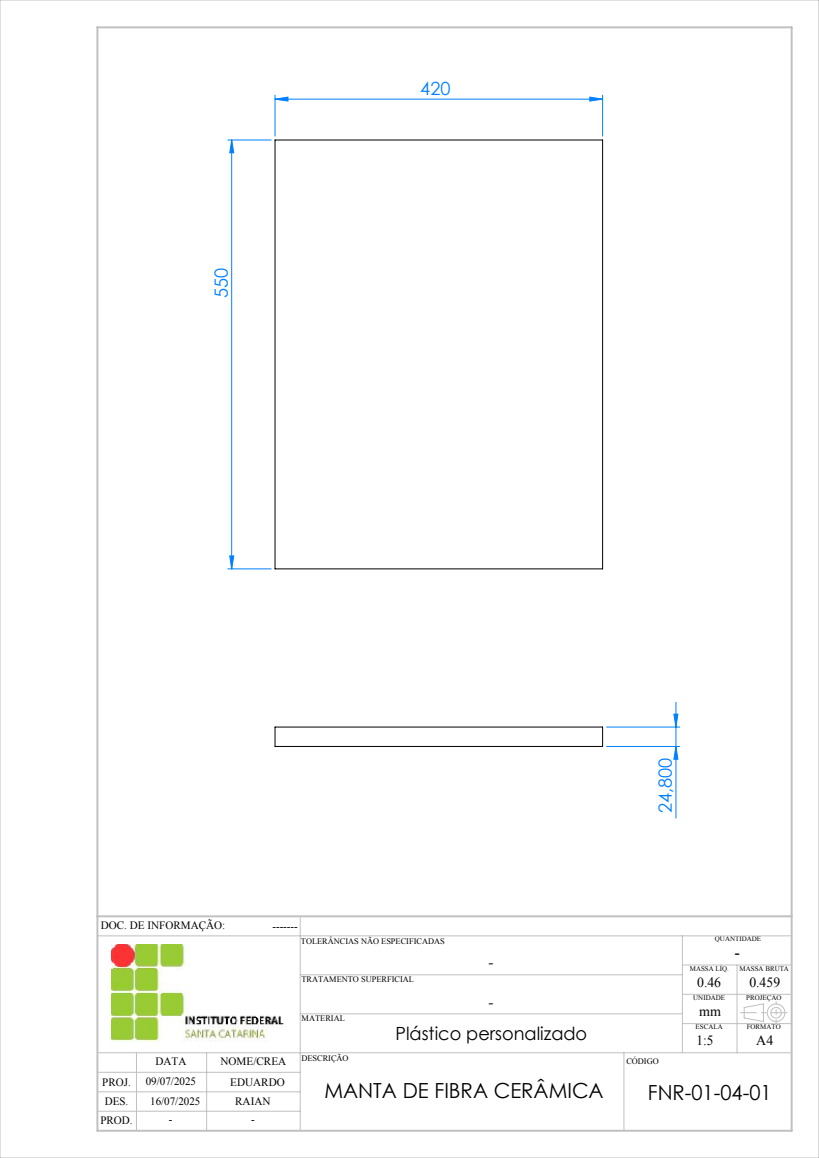
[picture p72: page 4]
Plástico personalizado; DATA; NOME/CREA DESCRIÇÃO; CÓDIGO; MATERIAL; TRATAMENTO SUPERFICIAL; ESCALA; FORMATO; UNIDADE; MASSA LÍQ.; QUANTIDADE; FNR-01-04-01 ⁰⁹/07/2025; MASSA BRUTA 0.459; PROJEÇÃO; RAIAN

DOC. DE INFORMAÇÃO:

TOLERÂNCIAS NÃO ESPECIFICADAS

MANTA DE FIBRA CERÂMICA

115

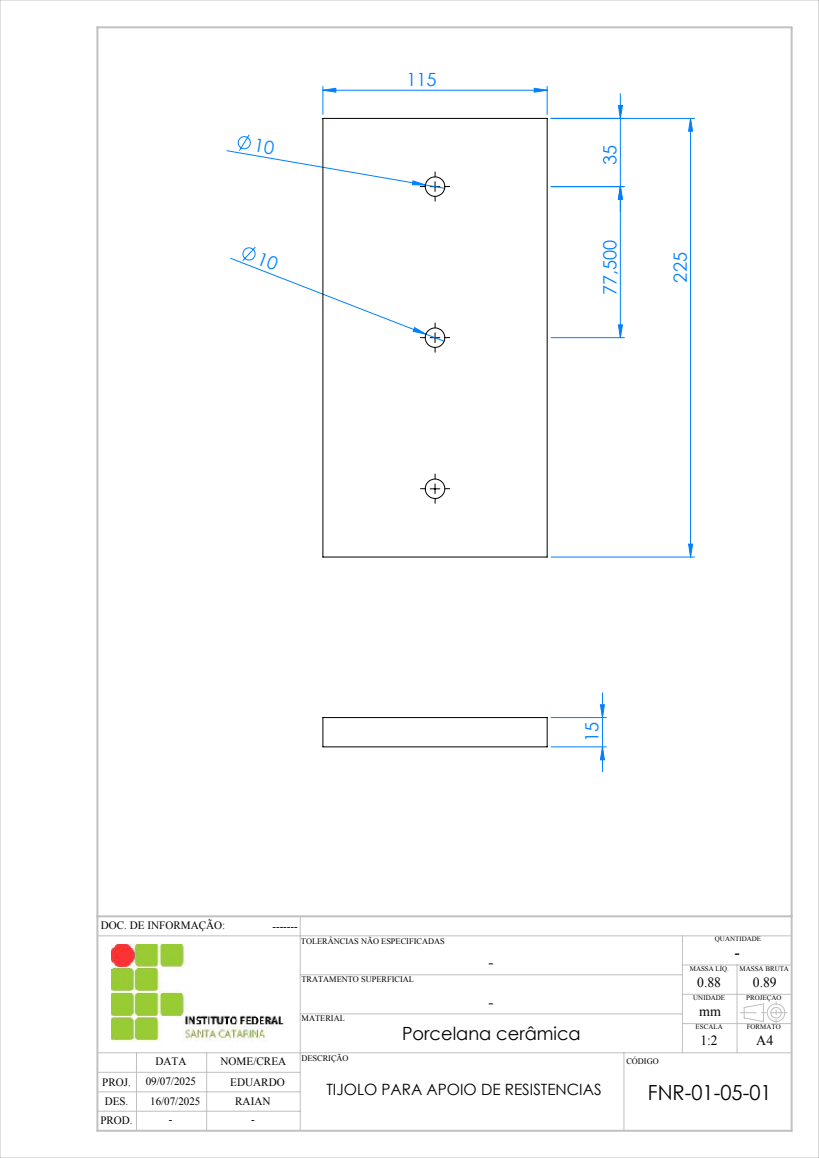
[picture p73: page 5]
Porcelana cerâmica; DATA; NOME/CREA DESCRIÇÃO; CÓDIGO; MATERIAL; TRATAMENTO SUPERFICIAL; ESCALA; FORMATO; UNIDADE; MASSA LÍQ.; QUANTIDADE; FNR-01-05-01 ⁰⁹/07/2025; MASSA BRUTA 0.89; PROJEÇÃO; RAIAN

DOC. DE INFORMAÇÃO:

TOLERÂNCIAS NÃO ESPECIFICADAS

TIJOLO PARA APOIO DE RESISTENCIAS

65

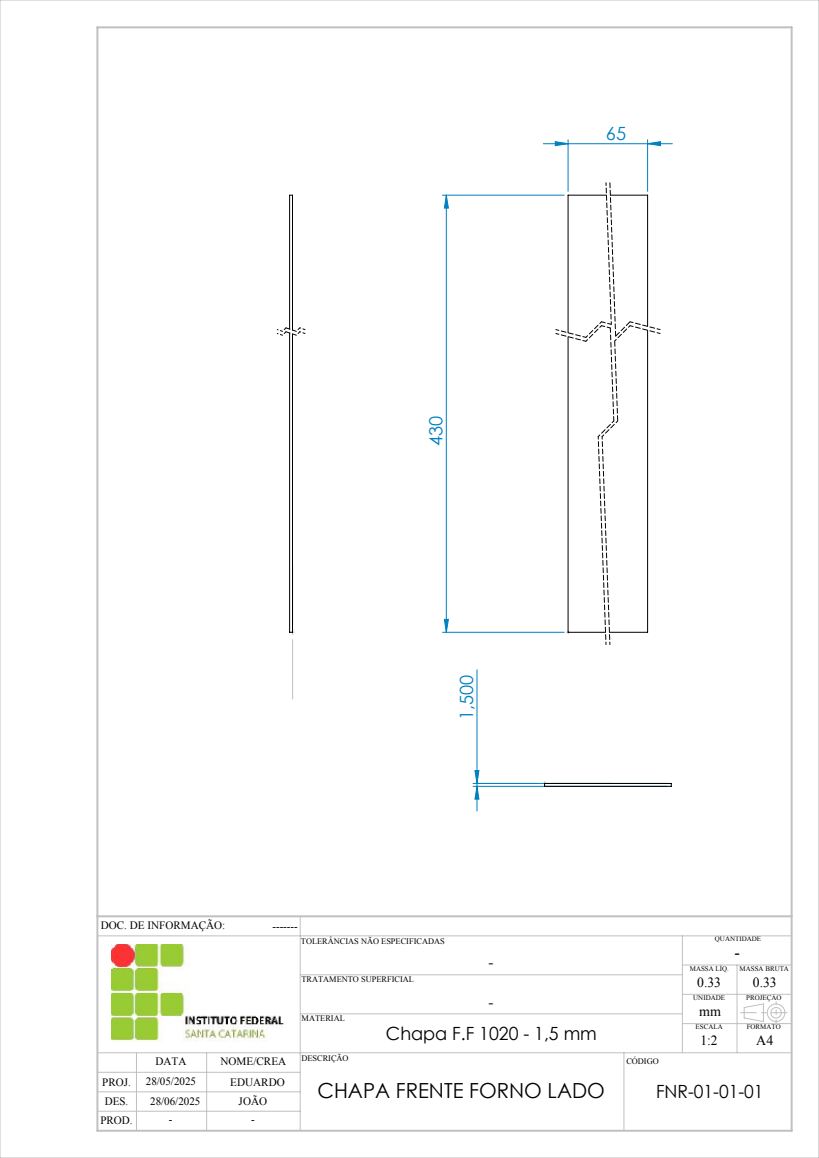
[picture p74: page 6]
Chapa F.F 1020 - 1,5 mm; DATA; NOME/CREA DESCRIÇÃO; CÓDIGO; MATERIAL; TRATAMENTO SUPERFICIAL; ESCALA; FORMATO; UNIDADE; MASSA LÍQ.; QUANTIDADE; FNR-01-01-01 ²⁸/05/2025; MASSA BRUTA 0.33; PROJEÇÃO; JOÃO

DOC. DE INFORMAÇÃO:

TOLERÂNCIAS NÃO ESPECIFICADAS

CHAPA FRENTE FORNO LADO

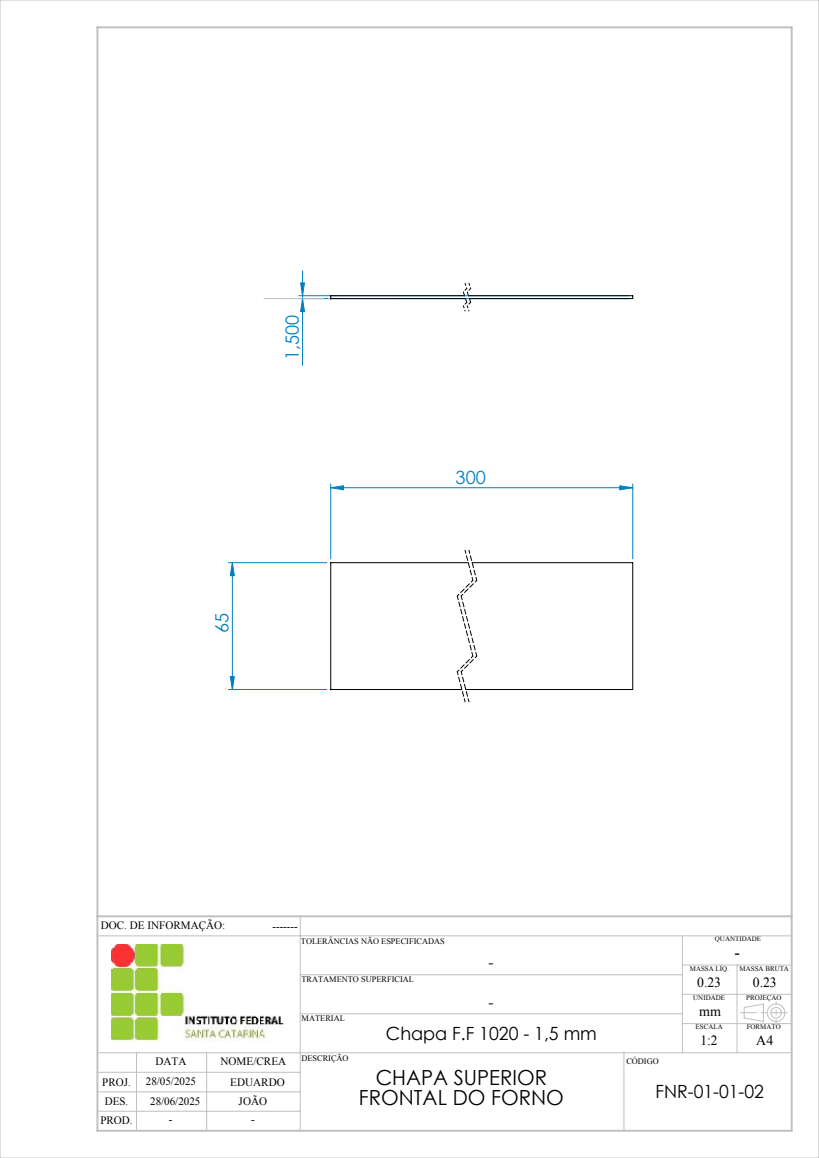
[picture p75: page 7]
Chapa F.F 1020 - 1,5 mm; DATA; NOME/CREA DESCRIÇÃO; CÓDIGO; TRATAMENTO SUPERFICIAL; ESCALA; FORMATO; UNIDADE; MASSA LÍQ.; QUANTIDADE; FNR-01-01-02 ²⁸/05/2025; MASSA BRUTA 0.23; PROJEÇÃO; JOÃO

DOC. DE INFORMAÇÃO:

TOLERÂNCIAS NÃO ESPECIFICADAS

MATERIAL
CHAPA SUPERIOR
FRONTAL DO FORNO

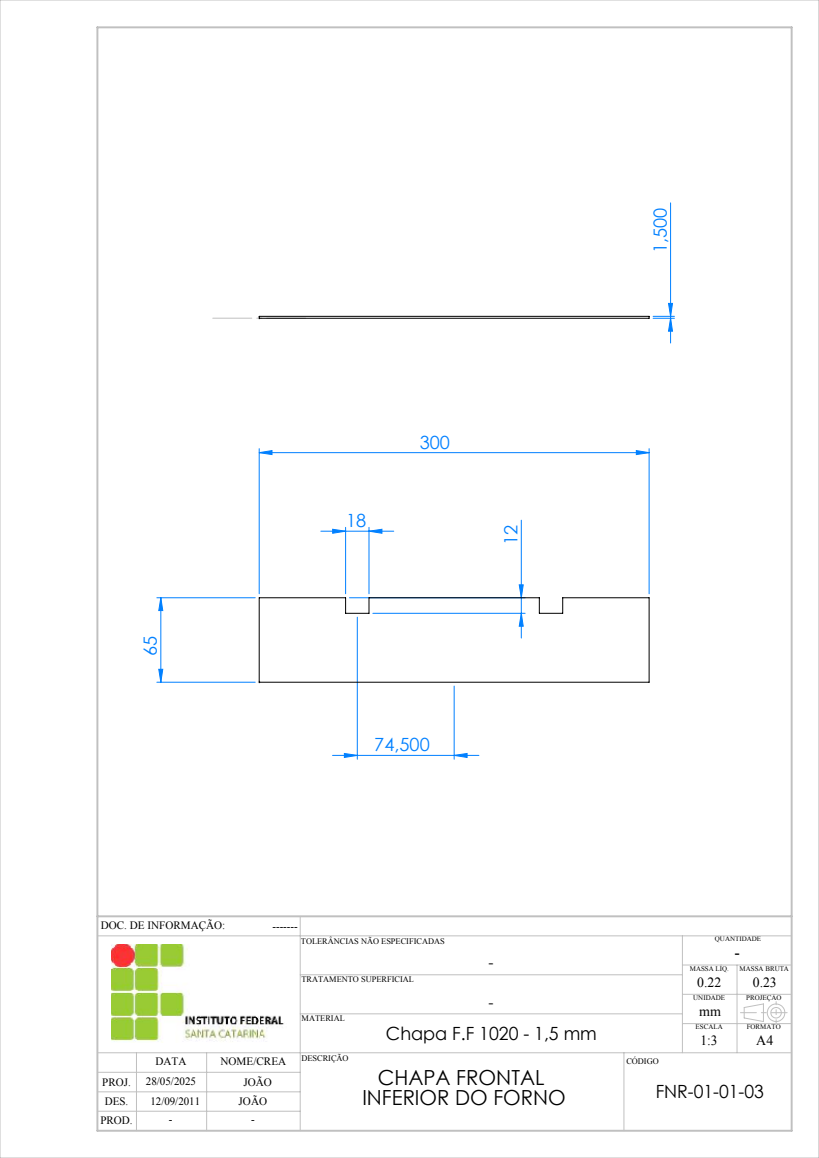
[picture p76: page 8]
Chapa F.F 1020 - 1,5 mm; DATA; NOME/CREA DESCRIÇÃO; CÓDIGO; TRATAMENTO SUPERFICIAL; ESCALA; FORMATO; UNIDADE; MASSA LÍQ.; QUANTIDADE; JOÃO; FNR-01-01-03 ²⁸/05/2025; MASSA BRUTA 0.23; PROJEÇÃO

DOC. DE INFORMAÇÃO:

TOLERÂNCIAS NÃO ESPECIFICADAS

MATERIAL
CHAPA FRONTAL
INFERIOR DO FORNO

1 | 2

1

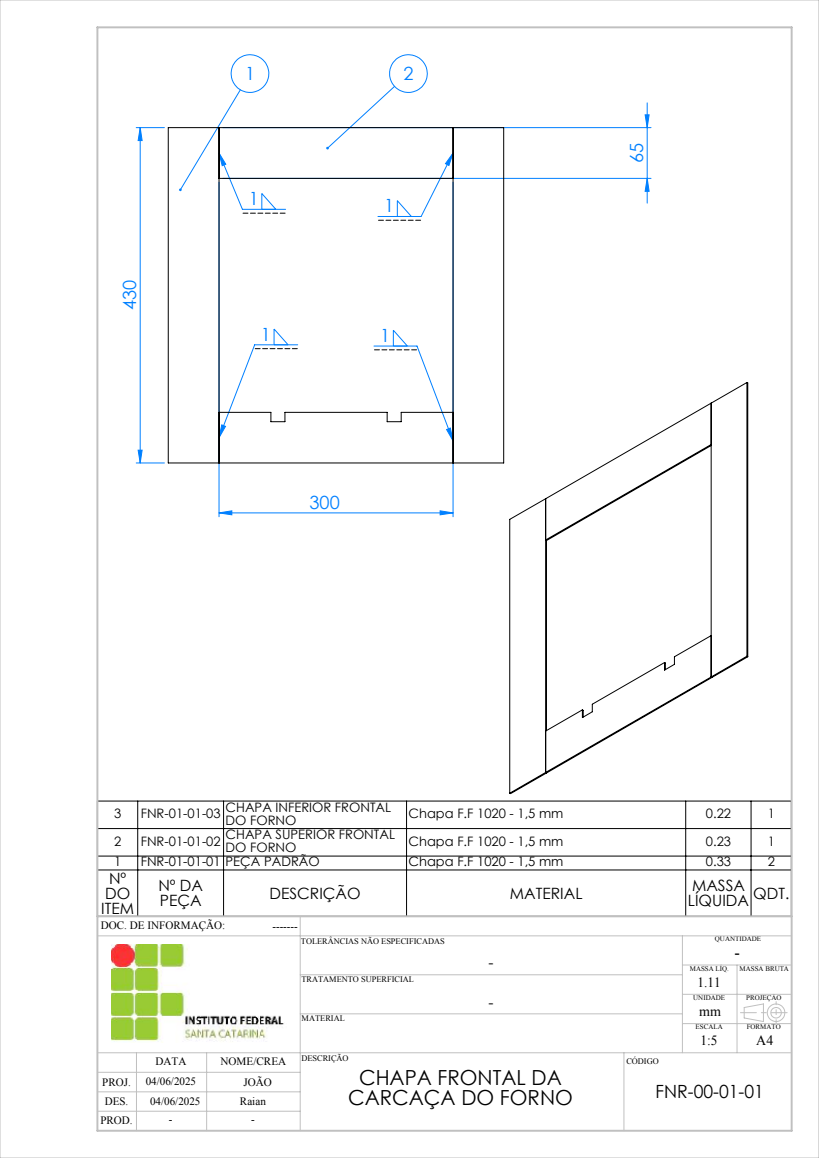
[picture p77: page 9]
DATA; NOME/CREA DESCRIÇÃO; CÓDIGO; TRATAMENTO SUPERFICIAL; ESCALA; FORMATO; UNIDADE; MASSA LÍQ.; QUANTIDADE; JOÃO; FNR-00-01-01 ⁰⁴/06/2025; MASSA BRUTA; PROJEÇÃO; Raian

3 | FNR-01-01-03 CHAPA INFERIOR FRONTAL | DO FORNO | Chapa F.F 1020 - 1,5 mm | 0.22 | 1
2 | FNR-01-01-02 CHAPA SUPERIOR FRONTAL | DO FORNO | Chapa F.F 1020 - 1,5 mm | 0.23 | 1
1 | FNR-01-01-01 PEÇA PADRÃO | | Chapa F.F 1020 - 1,5 mm | 0.33 | 2
Nº DO ITEM | Nº DA PEÇA | DESCRIÇÃO | MATERIAL | MASSA LÍQUIDA QDT.

DOC. DE INFORMAÇÃO:

TOLERÂNCIAS NÃO ESPECIFICADAS

MATERIAL
CHAPA FRONTAL DA
CARCAÇA DO FORNO

550

2

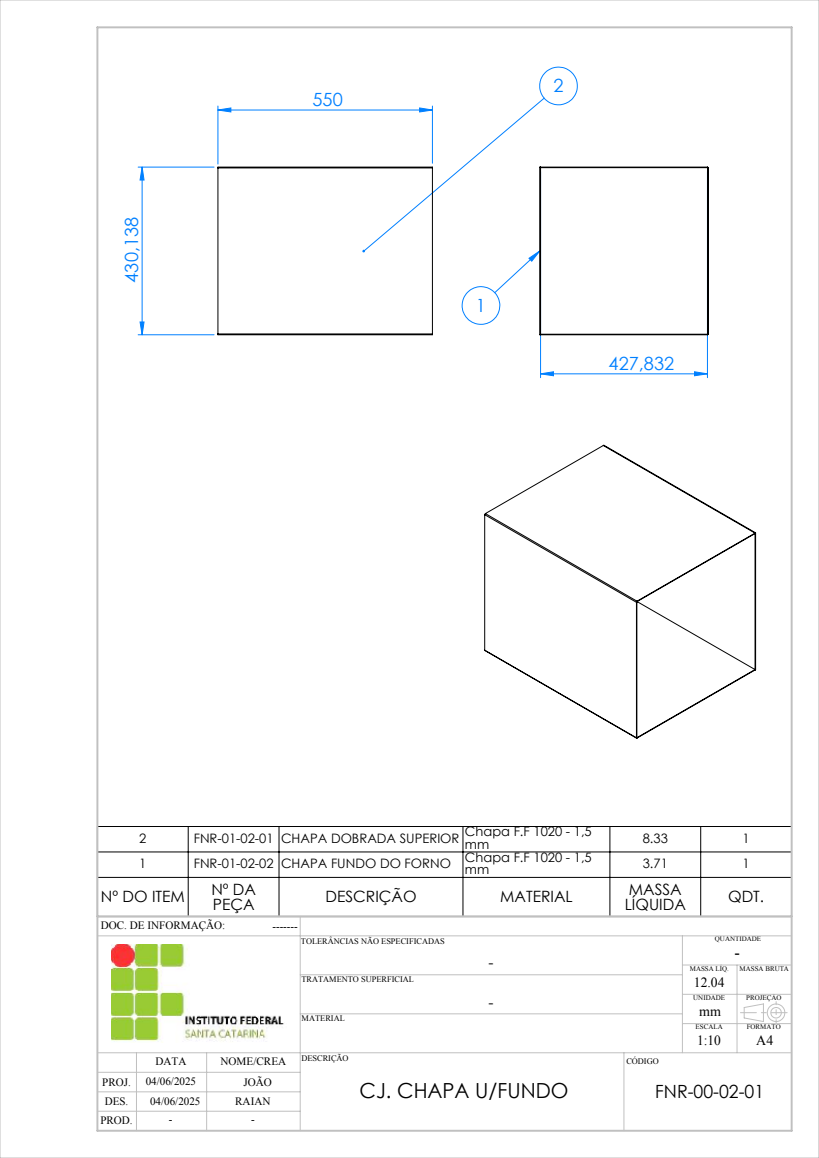
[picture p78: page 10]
DATA; NOME/CREA DESCRIÇÃO; CÓDIGO; MATERIAL; TRATAMENTO SUPERFICIAL; ESCALA; FORMATO; UNIDADE; MASSA LÍQ.; QUANTIDADE; JOÃO; MASSA BRUTA; PROJEÇÃO; RAIAN

2 | FNR-01-02-01 | CHAPA DOBRADA SUPERIOR | Chapa F.F 1020 - 1,5 mm | 8.33 | 1
1 | FNR-01-02-02 | CHAPA FUNDO DO FORNO | Chapa F.F 1020 - 1,5 mm | 3.71 | 1
Nº DO ITEM | Nº DA PEÇA | DESCRIÇÃO | MATERIAL | MASSA LÍQUIDA | QDT.

DOC. DE INFORMAÇÃO:

TOLERÂNCIAS NÃO ESPECIFICADAS

FNR-00-02-01 ⁰⁴/06/2025
CJ. CHAPA U/FUNDO PROJ.

A

1

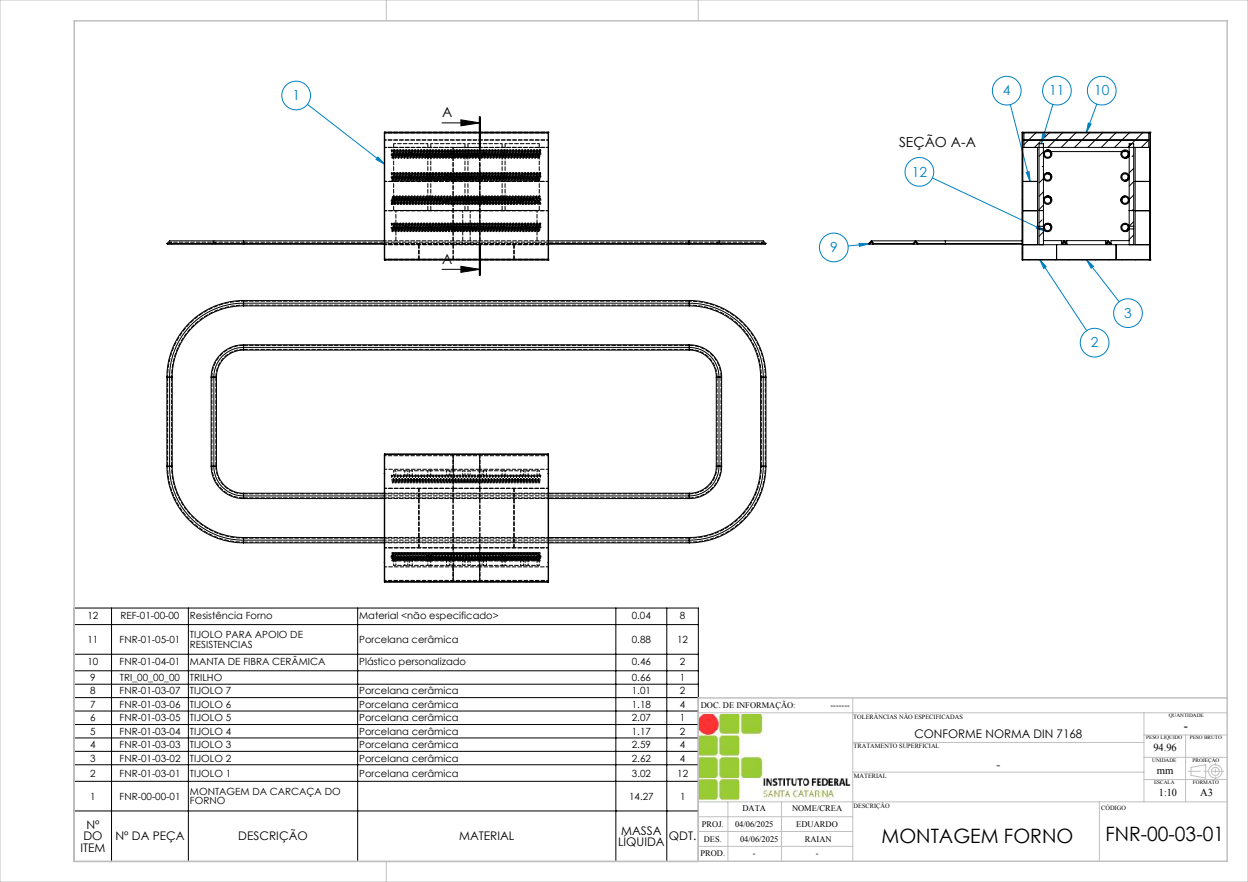
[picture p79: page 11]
SEÇÃO A-A; MATERIAL

12 | REF-01-00-00 | Resistência Forno | Material <não especificado> | 0.04 | 8
11 | FNR-01-05-01 | TIJOLO PARA APOIO DE RESISTENCIAS | Porcelana cerâmica | 0.88 | 12

10 | FNR-01-04-01 | MANTA DE FIBRA CERÂMICA | Plástico personalizado | 0.46 | 2
9 | TRI_00_00_00 | TRILHO | | 0.66 | 1
8 | FNR-01-03-07 | TIJOLO 7 | Porcelana cerâmica | 1.01 | 2
7 | FNR-01-03-06 | TIJOLO 6 | Porcelana cerâmica | 1.18 | 4 | DOC. DE INFORMAÇÃO: -------QUANTIDADE TOLERÂNCIAS NÃO ESPECIFICADAS CONFORME NORMA DIN 7168 -PESO LIQUIDO PESO BRUTO TRATAMENTO SUPERFICIAL 94.96 UNIDADE PROJEÇÃO ESCALA FORMATO 1:10 A3 DATA NOME/CREA DESCRIÇÃO CÓDIGO 04/06/2025 MONTAGEM FORNO FNR-00-03-01 PROJ. 04/06/2025 RAIAN --
6 | FNR-01-03-05 | TIJOLO 5 | Porcelana cerâmica | 2.07 | 1
5 | FNR-01-03-04 | TIJOLO 4 | Porcelana cerâmica | 1.17 | 2
4 | FNR-01-03-03 | TIJOLO 3 | Porcelana cerâmica | 2.59 | 4
3 | FNR-01-03-02 | TIJOLO 2 | Porcelana cerâmica | 2.62 | 4
2 | FNR-01-03-01 | TIJOLO 1 | Porcelana cerâmica | 3.02 | 12
1 | FNR-00-00-01 | MONTAGEM DA CARCAÇA DO FORNO | | 14.27 | 1

Nº DO ITEM | Nº DA PEÇA | DESCRIÇÃO | MATERIAL | LÍQUIDA QDT. MASSA

# Cordão de solda de 1mm em toda a borda do forno

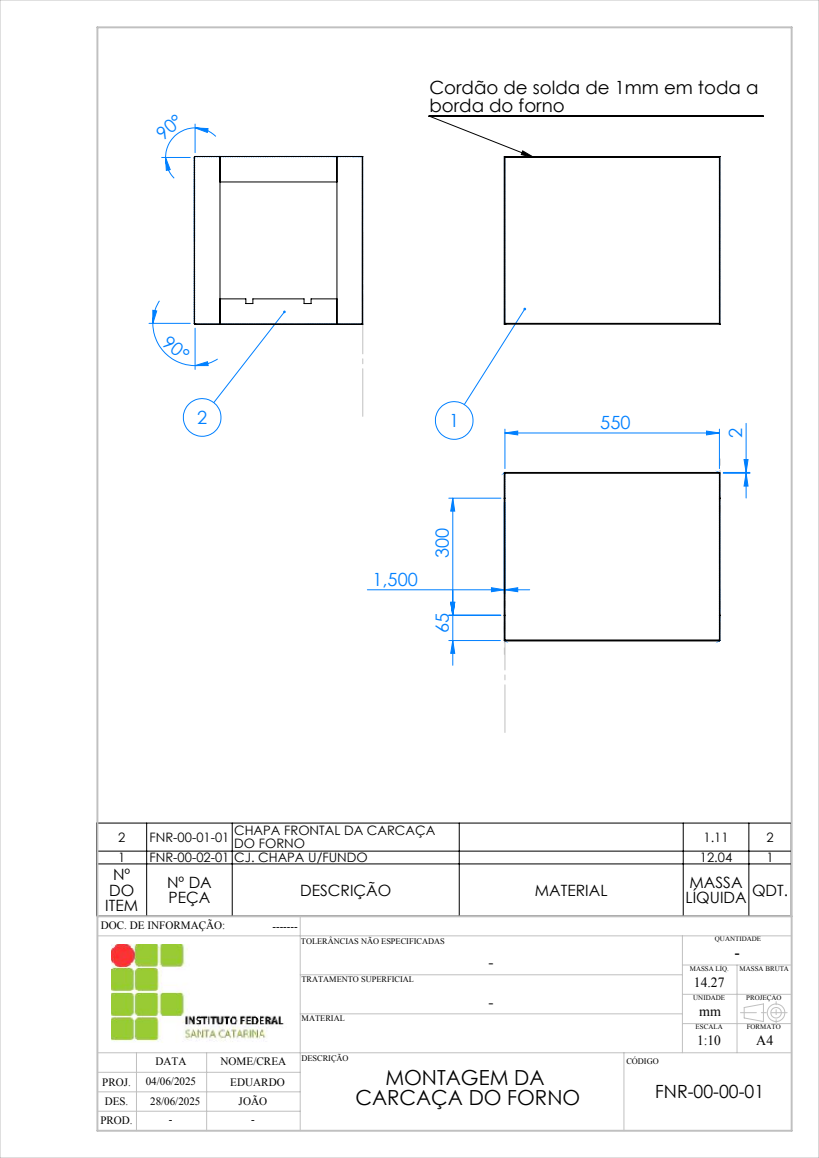
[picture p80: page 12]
DATA; NOME/CREA DESCRIÇÃO; CÓDIGO; TRATAMENTO SUPERFICIAL; ESCALA; FORMATO; UNIDADE; MASSA LÍQ.; QUANTIDADE; FNR-00-00-01 ⁰⁴/06/2025; MASSA BRUTA; PROJEÇÃO; JOÃO

2 | FNR-00-01-01 CHAPA FRONTAL DA CARCAÇA | DO FORNO | | 1.11 | 2
1 | FNR-00-02-01 CJ. CHAPA U/FUNDO | | | 12.04 | 1
Nº DO ITEM | Nº DA PEÇA | DESCRIÇÃO | MATERIAL | MASSA LÍQUIDA QDT.

DOC. DE INFORMAÇÃO:

TOLERÂNCIAS NÃO ESPECIFICADAS

MATERIAL
MONTAGEM DA
CARCAÇA DO FORNO

2
2

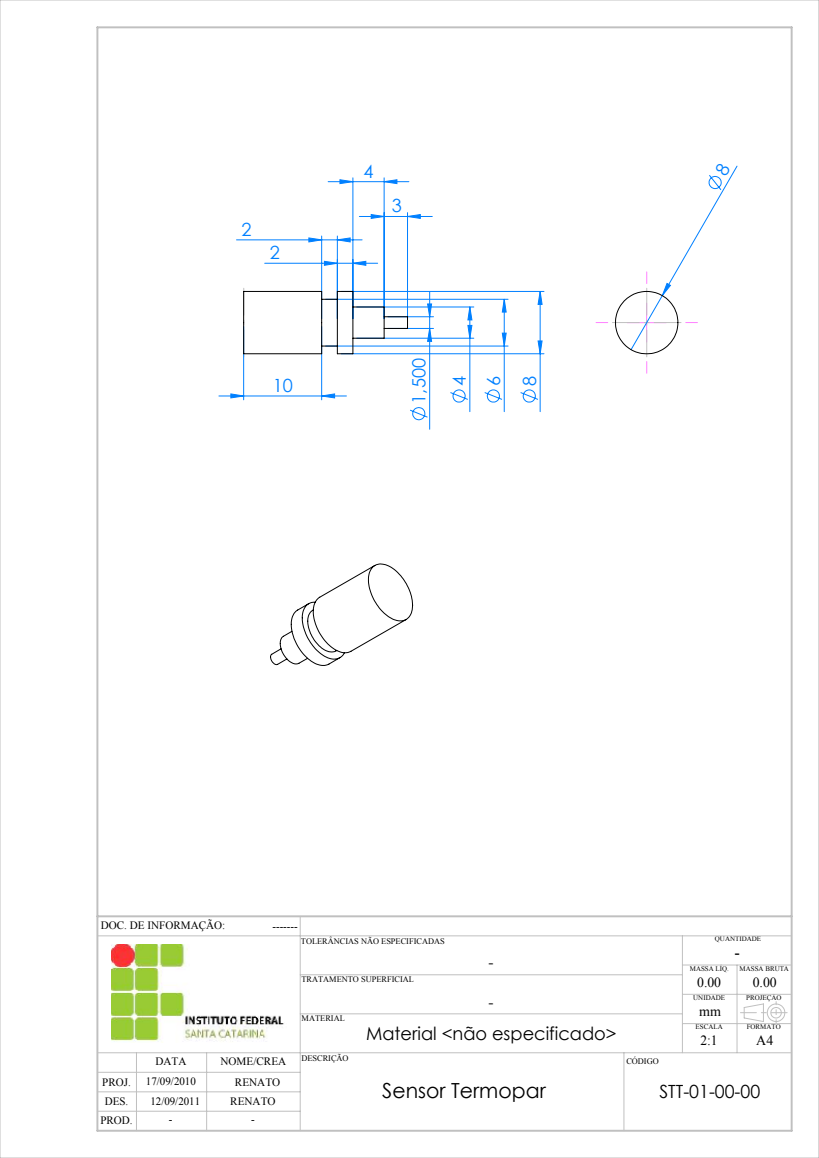
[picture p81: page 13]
Sensor Termopar; DATA; NOME/CREA DESCRIÇÃO; CÓDIGO; TRATAMENTO SUPERFICIAL; ESCALA; FORMATO; UNIDADE; MASSA LÍQ.; QUANTIDADE; RENATO; STT-01-00-00 ¹⁷/09/2010; MASSA BRUTA 0.00; PROJEÇÃO

DOC. DE INFORMAÇÃO:

TOLERÂNCIAS NÃO ESPECIFICADAS

MATERIAL
Material <não especificado>

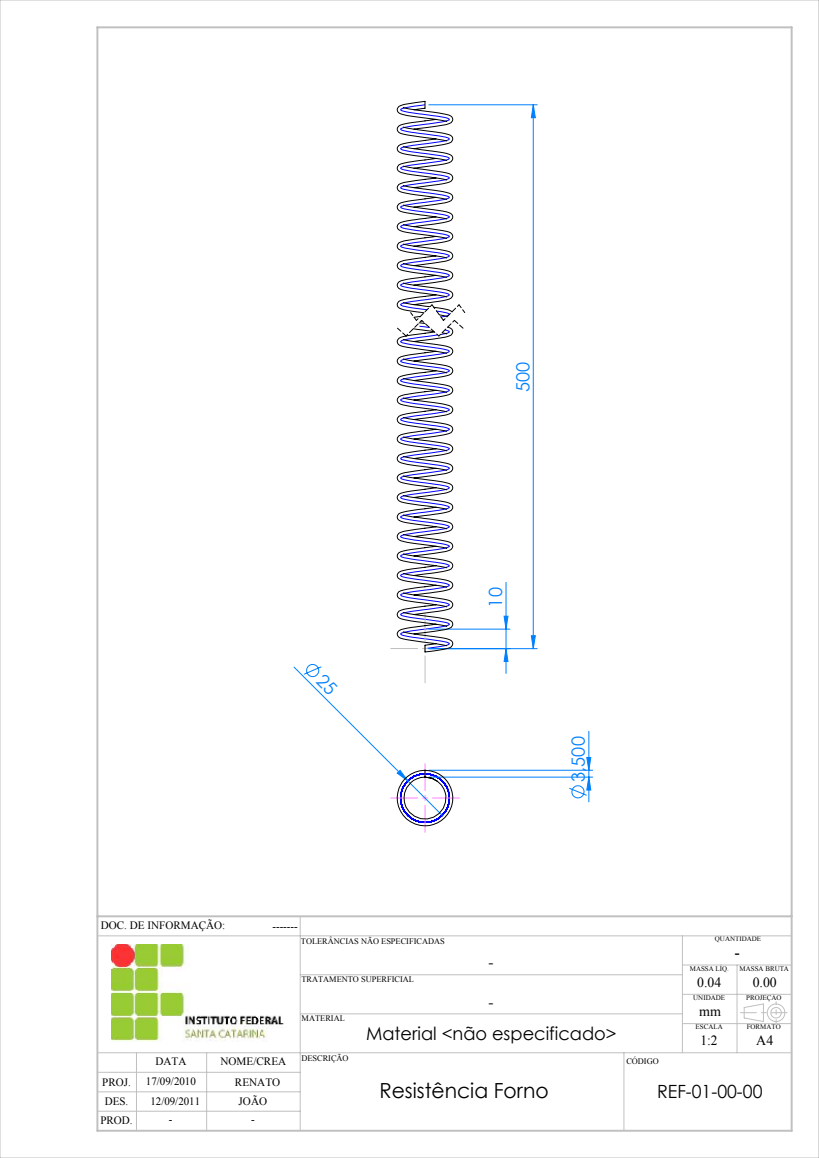
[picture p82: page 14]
Resistência Forno; DATA; NOME/CREA DESCRIÇÃO; CÓDIGO; TRATAMENTO SUPERFICIAL; ESCALA; FORMATO; UNIDADE; MASSA LÍQ.; QUANTIDADE; RENATO; REF-01-00-00 ¹⁷/09/2010; MASSA BRUTA 0.00; PROJEÇÃO; JOÃO

DOC. DE INFORMAÇÃO:

TOLERÂNCIAS NÃO ESPECIFICADAS

MATERIAL
Material <não especificado>

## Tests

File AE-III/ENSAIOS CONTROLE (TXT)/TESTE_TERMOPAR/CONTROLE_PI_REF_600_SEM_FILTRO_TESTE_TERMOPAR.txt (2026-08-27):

ets Jul 29 2019 12:21:46

rst:0x1 (POWERON_RESET),boot:0x12 (SPI_FAST_FLASH_BOOT)
configsip: 0, SPIWP:0xee
clk_drv:0x00,q_drv:0x00,d_drv:0x00,cs0_drv:0x00,hd_drv:0x00,wp_drv:0x00
mode:DIO, clock div:2
load:0x3fff0040,len:6272
load:0x40078000,len:15848
load:0x40080400,len:3920
entry 0x40080644
I (27) boot: ESP-IDF v6.0 2nd stage bootloader
I (27) boot: compile time Apr 23 2026 08:09:33
I (28) boot: Multicore bootloader
I (29) boot: chip revision: v3.1
I (31) boot.esp32: SPI Speed      : 40MHz
I (35) boot.esp32: SPI Mode       : DIO
I (39) boot.esp32: SPI Flash Size : 2MB
I (42) boot: Enabling RNG early entropy source...
I (47) boot: Partition Table:
I (49) boot: ## Label            Usage          Type ST Offset   Length
I (56) boot:  0 nvs              WiFi data        01 02 00009000 00006000
I (62) boot:  1 phy_init         RF data          01 01 0000f000 00001000
I (69) boot:  2 factory          factory app      00 00 00010000 00100000
I (75) boot: End of partition table
I (79) esp_image: segment 0: paddr=00010020 vaddr=3f400020 size=09658h ( 38488) map
I (100) esp_image: segment 1: paddr=00019680 vaddr=3ffb0000 size=02a2ch ( 10796) load
I (104) esp_image: segment 2: paddr=0001c0b4 vaddr=40080000 size=03f64h ( 16228) load
I (111) esp_image: segment 3: paddr=00020020 vaddr=400d0020 size=0f5d4h ( 62932) map
I (134) esp_image: segment 4: paddr=0002f5fc vaddr=40083f64 size=06e18h ( 28184) load
I (145) esp_image: segment 5: paddr=0003641c vaddr=50000000 size=00028h (    40) load
I (151) boot: Loaded app from partition at offset 0x10000
I (152) boot: Disabling RNG early entropy source...
I (164) cpu_start: Multicore app
I (172) cpu_start: GPIO 3 and 1 are used as console UART I/O pins
I (172) cpu_start: Pro cpu start user code
I (172) cpu_start: cpu freq: 160000000 Hz
I (174) app_init: Application information:
I (178) app_init: Project name:     app-template
I (182) app_init: App version:      1
I (186) app_init: Compile time:     Apr 23 2026 08:07:59
I (191) app_init: ELF file SHA256:  187407ae9...
I (195) app_init: ESP-IDF:          v6.0
I (199) efuse_init: Min chip rev:     v0.0
I (202) efuse_init: Max chip rev:     v3.99 
I (206) efuse_init: Chip rev:         v3.1
I (211) heap_init: Initializing. RAM available for dynamic allocation:
I (217) heap_init: At 3FFAE6E0 len 00001920 (6 KiB): DRAM
I (222) heap_init: At 3FFB3410 len 0002CBF0 (178 KiB): DRAM
I (227) heap_init: At 3FFE0440 len 00003AE0 (14 KiB): D/IRAM
I (232) heap_init: At 3FFE4350 len 0001BCB0 (111 KiB): D/IRAM
I (238) heap_init: At 4008AD7C len 00015284 (84 KiB): IRAM
I (245) spi_flash: detected chip: generic
I (247) spi_flash: flash io: dio
W (250) spi_flash: Detected size(4096k) larger than the size in the binary image header(2048k). Using the size in the binary image header.
I (263) main_task: Started on CPU0
I (273) main_task: Calling app_main()
1,1604,41.64,0.000000 
2,1604,41.64,9.235869 
3,1601,40.04,9.237197 
4,1602,40.57,9.265125 
5,1600,39.50,9.257590 
6,1595,36.82,9.276654 
7,1600,39.50,9.322321 
8,1588,33.07,9.279327 
9,1598,38.43,9.387060 
10,1600,39.50,9.299742 
11,1596,37.36,9.283344 
Forno LIGADOForno LIGADOForno LIGADOForno LIGADOForno LIGADOForno LIGADOForno LIGADOForno LIGADOForno LIGADOForno LIGADOForno LIGADOForno LIGADOForno LIGADOForno LIGADO12,1600,39.50,9.320144 
13,1600,39.50,9.286016 
14,1600,39.50,9.287349 
15,1594,36.28,9.288682 
16,1579,28.24,9.343215 
17,1603,41.11,9.477556 
18,1598,38.43,9.266115 
19,1591,34.68,9.311778 
20,1559,17.52,9.375181 
21,1602,40.57,9.660259 
22,1607,43.25,9.280377 
23,1604,41.64,9.237374 
24,1605,42.18,9.265299 
25,1602,40.57,9.257760 
26,1648,65.23,9.285686 
27,1606,42.72,8.879150 
28,1601,40.04,9.252823 
29,1612,45.93,9.298481 
30,1613,46.47,9.202280 
31,1610,44.86,9.194731 
32,1614,47.00,9.222648 
33,1611,45.40,9.188501 
34,1616,48.08,9.216416 
35,1610,44.86,9.173402 
36,1613,46.47,9.227915 
37,1617,48.61,9.202636 
38,1603,41.11,9.168485 
39,1615,47.54,9.293930 
40,1616,48.08,9.188859 
41,1621,50.76,9.181307 
42,1616,48.08,9.138286 
43,1623,51.83,9.183926 
44,1621,50.76,9.123172 
45,1626,53.44,9.142209 
46,1622,51.29,9.099182 
47,1623,51.83,9.135948 
48,1622,51.29,9.128386 
49,1630,55.58,9.138557 
50,1629,55.05,9.068929 
51,1629,55.05,9.079090 
52,1637,59.33,9.080387 
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

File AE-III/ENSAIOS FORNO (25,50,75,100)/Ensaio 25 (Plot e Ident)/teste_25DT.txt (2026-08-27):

19,0,0.00
20,0,0.00
21,45,15.35
22,11,3.75
23,11,3.75
24,0,0.00
25,30,10.23
26,43,14.67
27,16,5.46
28,42,14.33
29,43,14.67
30,56,19.10
31,26,8.87
32,38,12.96
33,11,3.75
34,44,15.01
35,37,12.62
36,21,7.16
37,55,18.76
38,11,3.75
39,39,13.30
40,16,5.46
41,21,7.16
42,77,26.27
43,68,23.20
44,53,18.08
45,44,15.01
46,16,5.46
47,48,16.37
48,39,13.30
49,40,13.65
50,25,8.53
51,59,20.13
52,47,16.03
53,60,20.47
54,3,1.02
55,48,16.37
56,39,13.30
57,64,21.83
58,17,5.80
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

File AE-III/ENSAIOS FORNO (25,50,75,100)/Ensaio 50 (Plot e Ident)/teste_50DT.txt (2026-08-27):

10,67,22.86
11,45,15.35
12,45,15.35
13,35,11.94
14,95,32.41
15,80,27.29
16,66,22.51
17,54,18.42
18,28,9.55
19,38,12.96
20,86,29.34
21,43,14.67
22,53,18.08
23,31,10.57
24,55,18.76
25,46,15.69
26,0,0.00
27,78,26.61
28,49,16.72
29,59,20.13
30,60,20.47
31,38,12.96
32,34,11.60
33,74,25.24
34,80,27.29
35,67,22.86
36,56,19.10
37,94,32.07
38,86,29.34
39,55,18.76
40,59,20.13
41,82,27.97
42,58,19.79
43,104,35.48
44,59,20.13
45,48,16.37
46,110,37.52
47,91,31.04
48,76,25.93
49,114,38.89
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

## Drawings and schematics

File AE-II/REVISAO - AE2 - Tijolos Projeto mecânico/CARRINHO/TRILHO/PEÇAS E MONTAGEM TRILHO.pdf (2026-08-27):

6,732

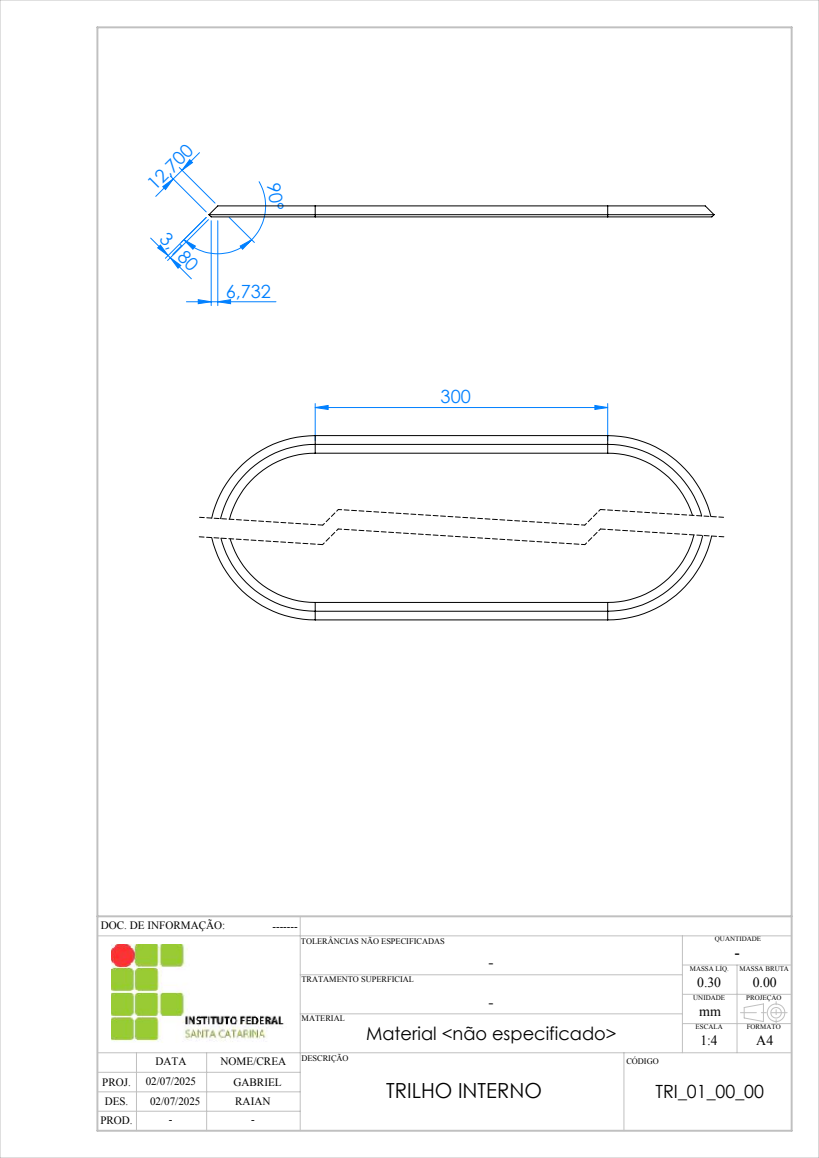
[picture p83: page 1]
TRILHO INTERNO; PROJ. DES. PROD.; DATA; NOME/CREA DESCRIÇÃO; CÓDIGO; TRATAMENTO SUPERFICIAL; ESCALA; FORMATO; UNIDADE; MASSA LÍQ.; QUANTIDADE; GABRIEL; TRI_01_00_00 ⁰²/07/2025; MASSA BRUTA 0.00; PROJEÇÃO; RAIAN

DOC. DE INFORMAÇÃO:

TOLERÂNCIAS NÃO ESPECIFICADAS

MATERIAL
Material <não especificado>

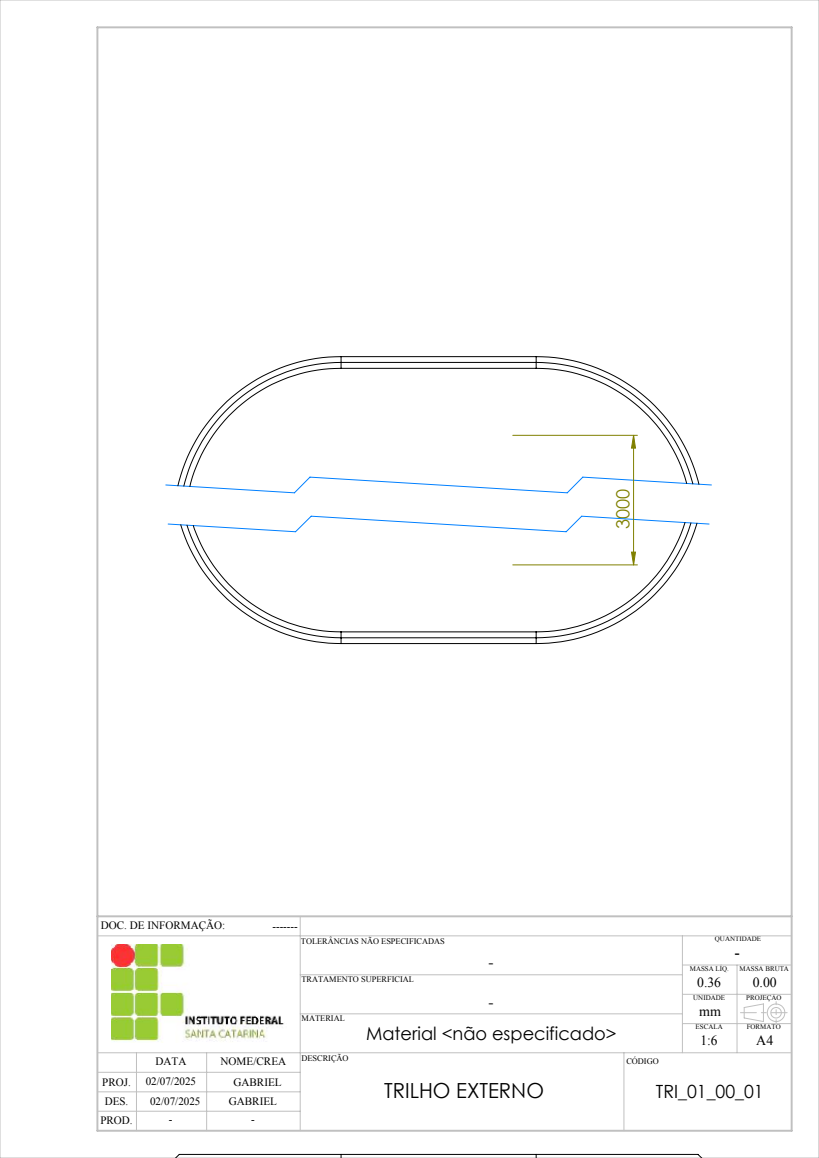
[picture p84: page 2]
TRILHO EXTERNO; PROJ.; DATA; NOME/CREA DESCRIÇÃO; CÓDIGO; TRATAMENTO SUPERFICIAL; ESCALA; FORMATO; UNIDADE; MASSA LÍQ.; QUANTIDADE; GABRIEL; TRI_01_00_01 ⁰²/07/2025; MASSA BRUTA 0.00; PROJEÇÃO

DOC. DE INFORMAÇÃO:

TOLERÂNCIAS NÃO ESPECIFICADAS

MATERIAL
Material <não especificado>

149

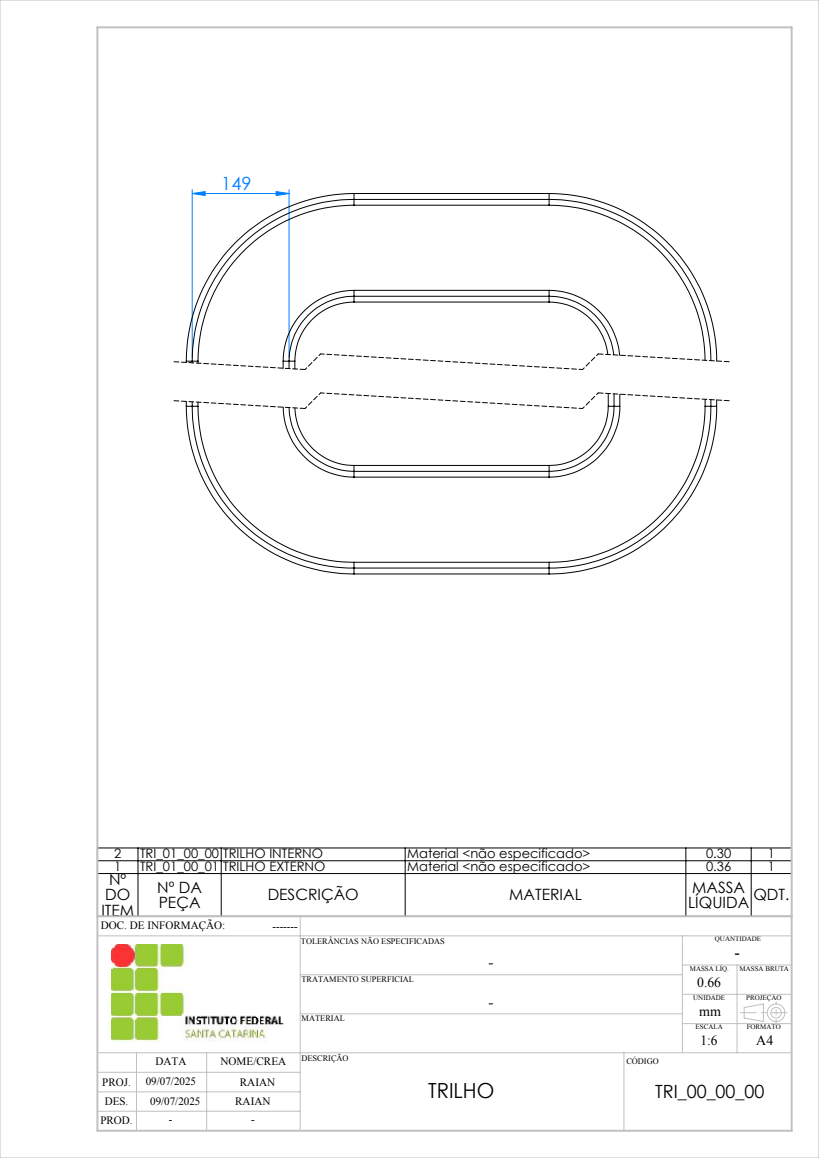
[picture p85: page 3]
TRILHO PROJ.; DATA; NOME/CREA DESCRIÇÃO; CÓDIGO; MATERIAL; TRATAMENTO SUPERFICIAL; ESCALA; FORMATO; UNIDADE; MASSA LÍQ.; QUANTIDADE; RAIAN; TRI_00_00_00 ⁰⁹/07/2025; MASSA BRUTA; PROJEÇÃO

2 | TRI_01_00_00 TRILHO INTERNO | | Material <não especificado> | 0.30 | 1
1 | TRI_01_00_01 TRILHO EXTERNO | | Material <não especificado> | 0.36 | 1
Nº DO ITEM | Nº DA PEÇA | DESCRIÇÃO | MATERIAL | MASSA LÍQUIDA QDT.

DOC. DE INFORMAÇÃO:

TOLERÂNCIAS NÃO ESPECIFICADAS

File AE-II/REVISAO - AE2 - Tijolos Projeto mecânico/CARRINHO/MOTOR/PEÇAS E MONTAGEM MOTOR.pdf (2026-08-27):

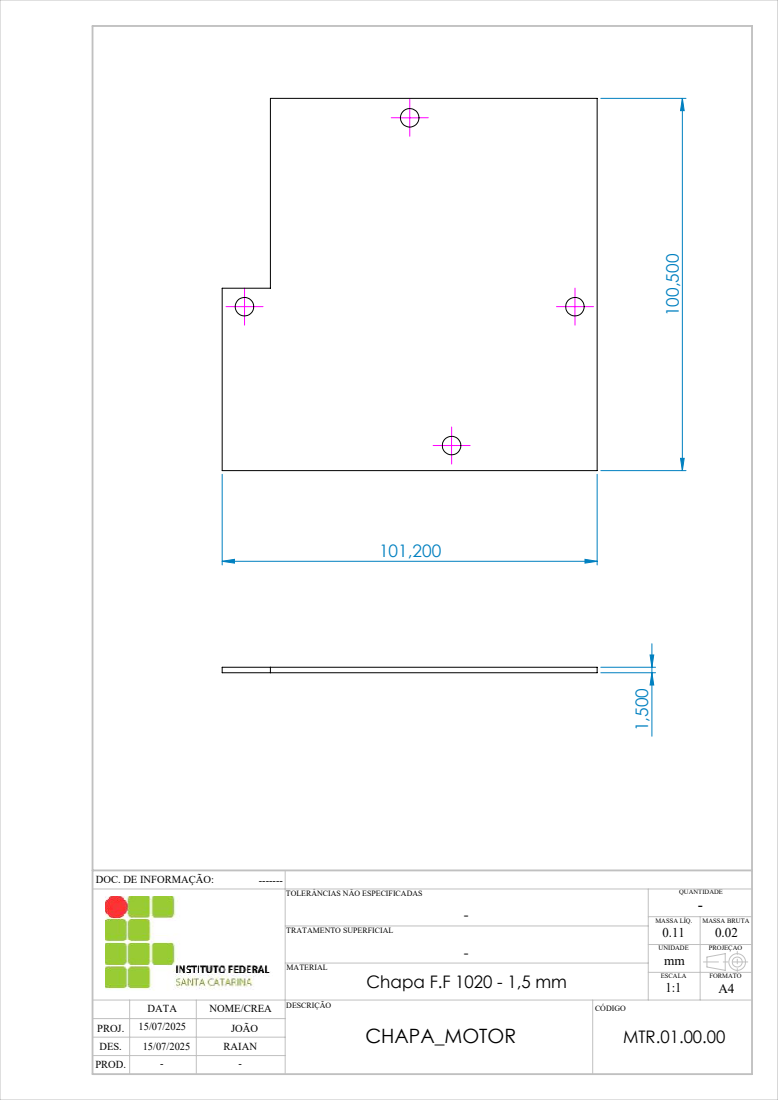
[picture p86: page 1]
CHAPA_MOTOR; Chapa F.F 1020 - 1,5 mm; PROJ. DES. PROD.; DATA; NOME/CREA DESCRIÇÃO; CÓDIGO; MATERIAL; TRATAMENTO SUPERFICIAL; ESCALA; FORMATO; UNIDADE; MASSA LÍQ.; QUANTIDADE; JOÃO; MTR.01.00.00 ¹⁵/07/2025; MASSA BRUTA 0.02; PROJEÇÃO; RAIAN

DOC. DE INFORMAÇÃO:

TOLERÂNCIAS NÃO ESPECIFICADAS

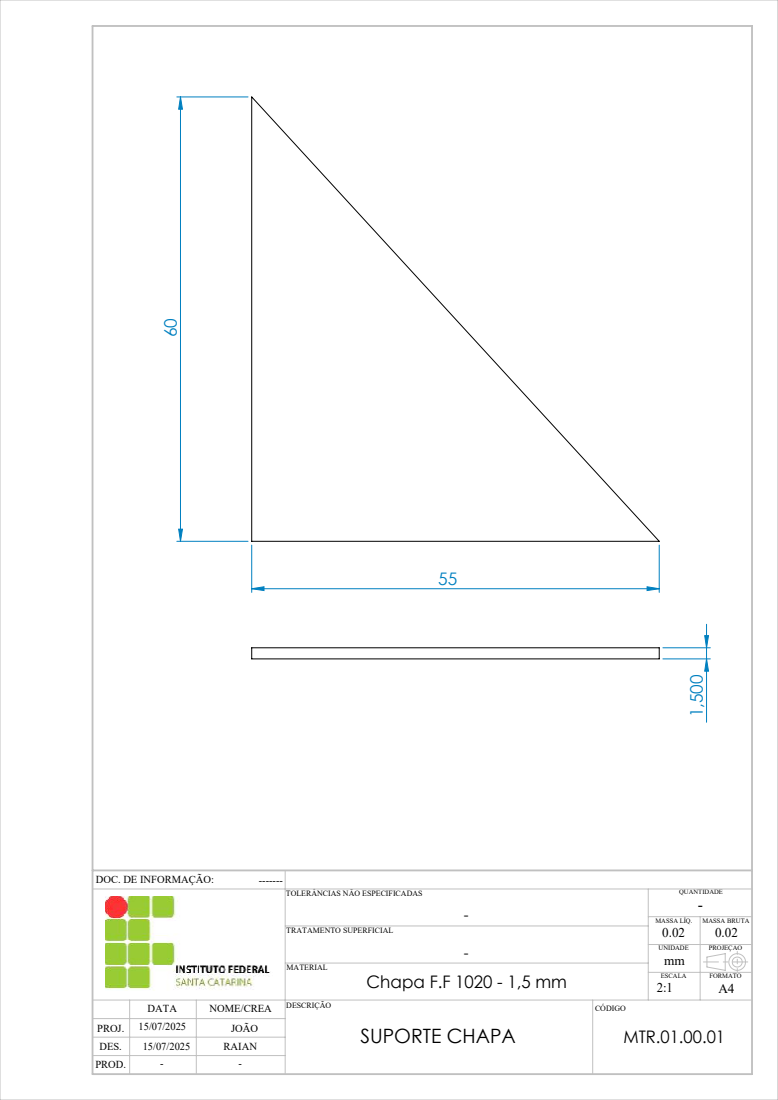
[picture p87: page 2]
SUPORTE CHAPA; Chapa F.F 1020 - 1,5 mm; DATA; NOME/CREA DESCRIÇÃO; CÓDIGO; MATERIAL; TRATAMENTO SUPERFICIAL; ESCALA; FORMATO; UNIDADE; MASSA LÍQ.; QUANTIDADE; MTR.01.00.01 ¹⁵/07/2025; MASSA BRUTA 0.02; PROJEÇÃO

DOC. DE INFORMAÇÃO:

TOLERÂNCIAS NÃO ESPECIFICADAS

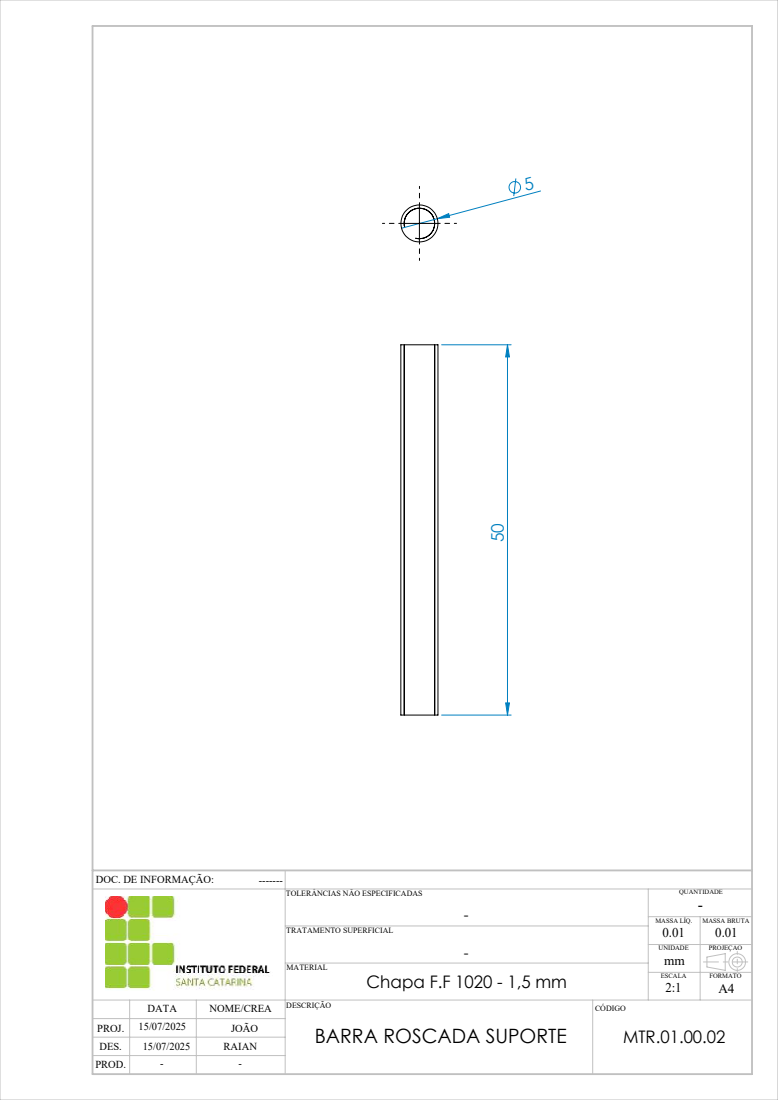
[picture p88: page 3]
Chapa F.F 1020 - 1,5 mm; DATA; NOME/CREA DESCRIÇÃO; CÓDIGO; MATERIAL; TRATAMENTO SUPERFICIAL; ESCALA; FORMATO; UNIDADE; MASSA LÍQ.; QUANTIDADE; MTR.01.00.02 ¹⁵/07/2025; MASSA BRUTA 0.01; PROJEÇÃO

DOC. DE INFORMAÇÃO:

TOLERÂNCIAS NÃO ESPECIFICADAS

BARRA ROSCADA SUPORTE

100 | R3

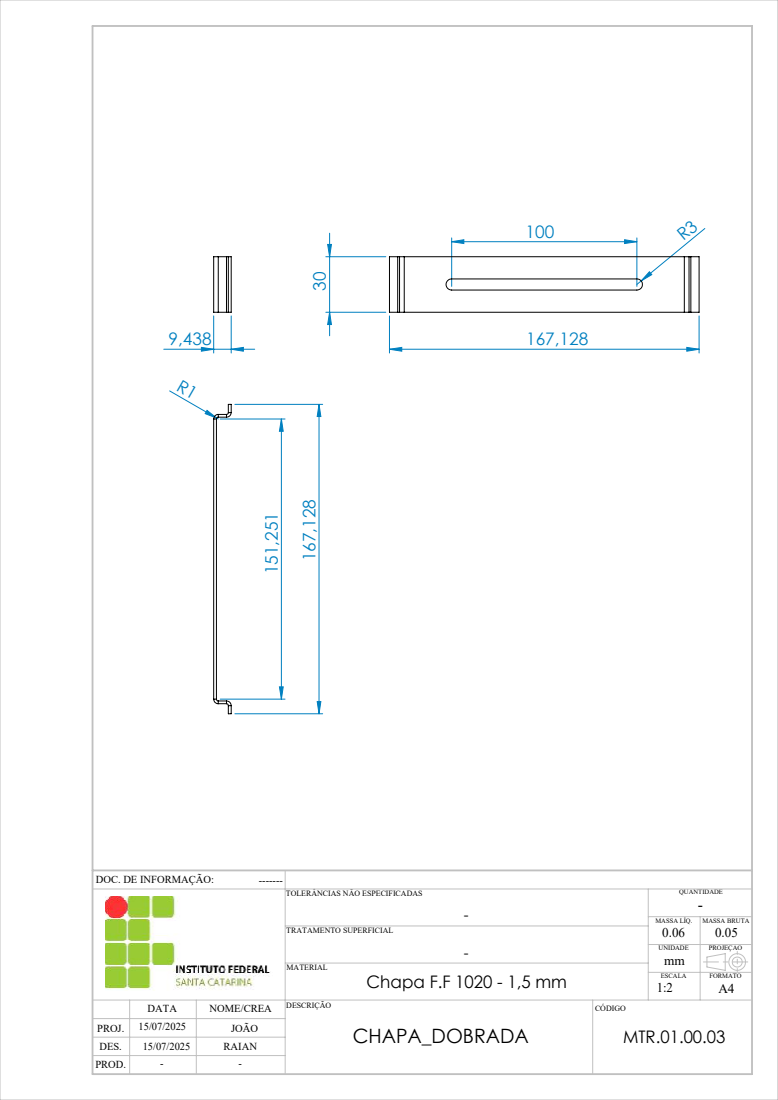
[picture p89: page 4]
CHAPA_DOBRADA; Chapa F.F 1020 - 1,5 mm; DATA; NOME/CREA DESCRIÇÃO; CÓDIGO; MATERIAL; TRATAMENTO SUPERFICIAL; ESCALA; FORMATO; UNIDADE; MASSA LÍQ.; QUANTIDADE; MTR.01.00.03 ¹⁵/07/2025; MASSA BRUTA 0.05; PROJEÇÃO

DOC. DE INFORMAÇÃO:

TOLERÂNCIAS NÃO ESPECIFICADAS

4

3

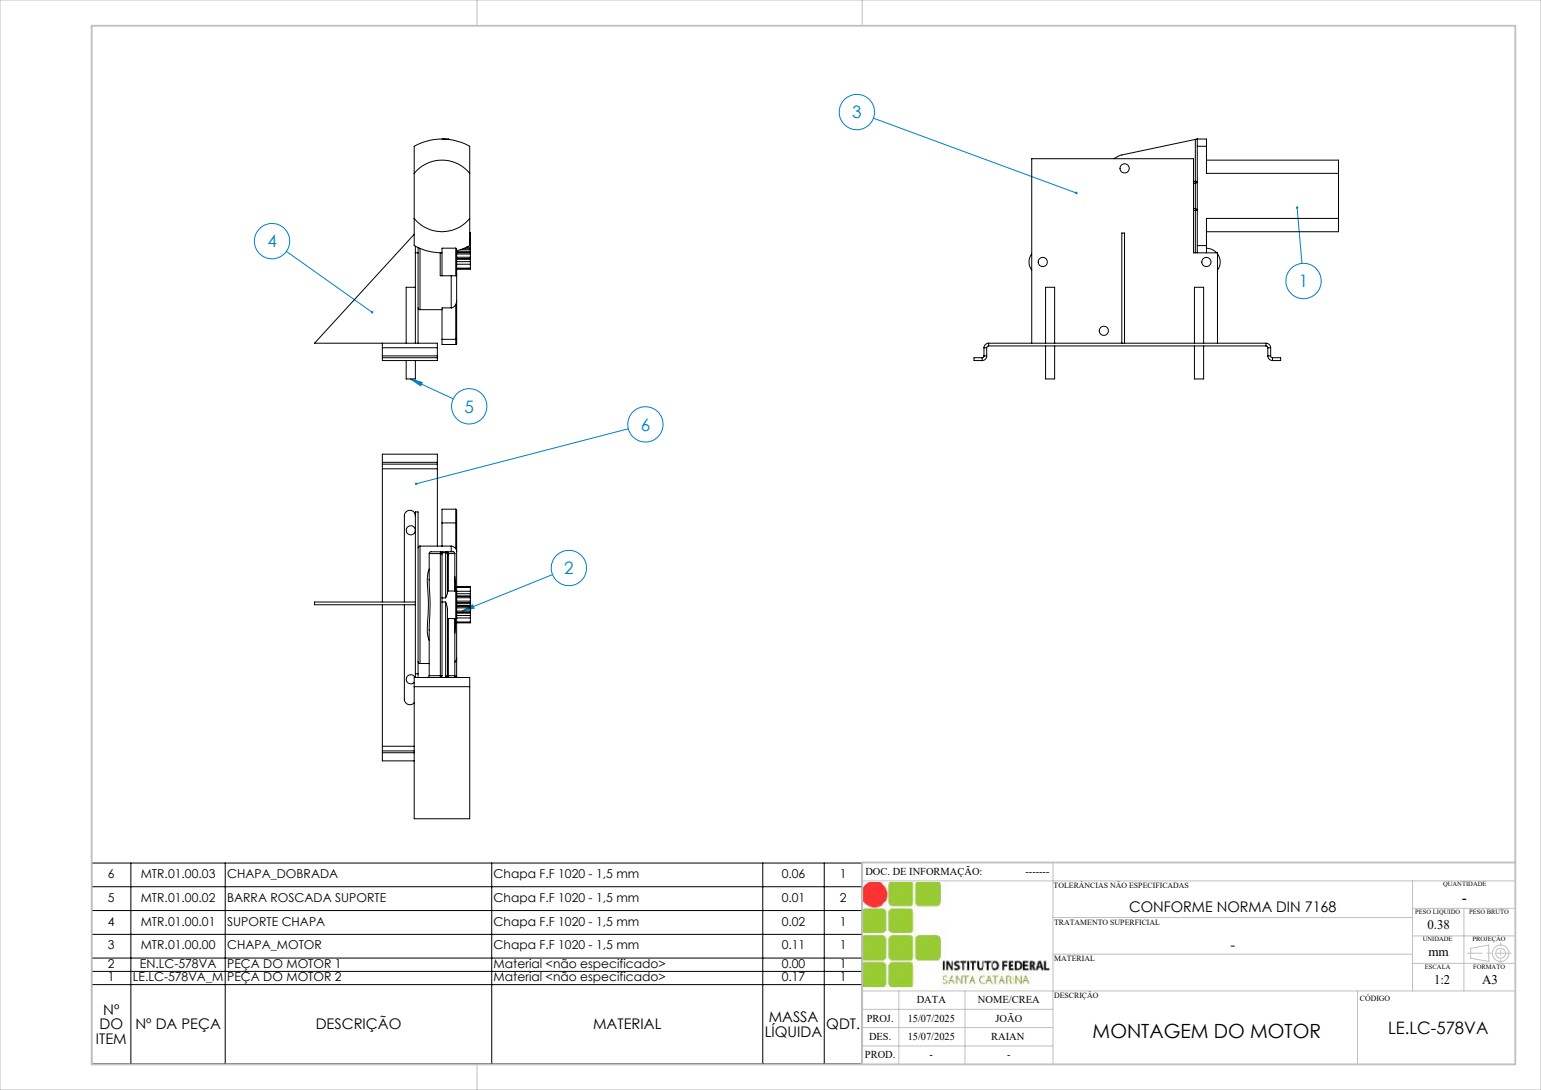
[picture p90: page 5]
MATERIAL

6 | MTR.01.00.03 | CHAPA_DOBRADA | Chapa F.F 1020 - 1,5 mm | 0.06 | 1 | DOC. DE INFORMAÇÃO: -------QUANTIDADE TOLERÂNCIAS NÃO ESPECIFICADAS CONFORME NORMA DIN 7168 -PESO LIQUIDO PESO BRUTO TRATAMENTO SUPERFICIAL 0.38 UNIDADE PROJEÇÃO ESCALA FORMATO 1:2 A3 DATA NOME/CREA DESCRIÇÃO CÓDIGO 15/07/2025 MONTAGEM DO MOTOR LE.LC-578VA PROJ. --
5 | MTR.01.00.02 | BARRA ROSCADA SUPORTE | Chapa F.F 1020 - 1,5 mm | 0.01 | 2
4 | MTR.01.00.01 | SUPORTE CHAPA | Chapa F.F 1020 - 1,5 mm | 0.02 | 1
3 | MTR.01.00.00 | CHAPA_MOTOR | Chapa F.F 1020 - 1,5 mm | 0.11 | 1
2 | EN.LC-578VA | PEÇA DO MOTOR 1 | Material <não especificado> | 0.00 | 1
1 | LE.LC-578VA_M PEÇA DO MOTOR 2 | | Material <não especificado> | 0.17 | 1
Nº DO ITEM | Nº DA PEÇA | DESCRIÇÃO | MATERIAL | MASSA LÍQUIDA QDT.

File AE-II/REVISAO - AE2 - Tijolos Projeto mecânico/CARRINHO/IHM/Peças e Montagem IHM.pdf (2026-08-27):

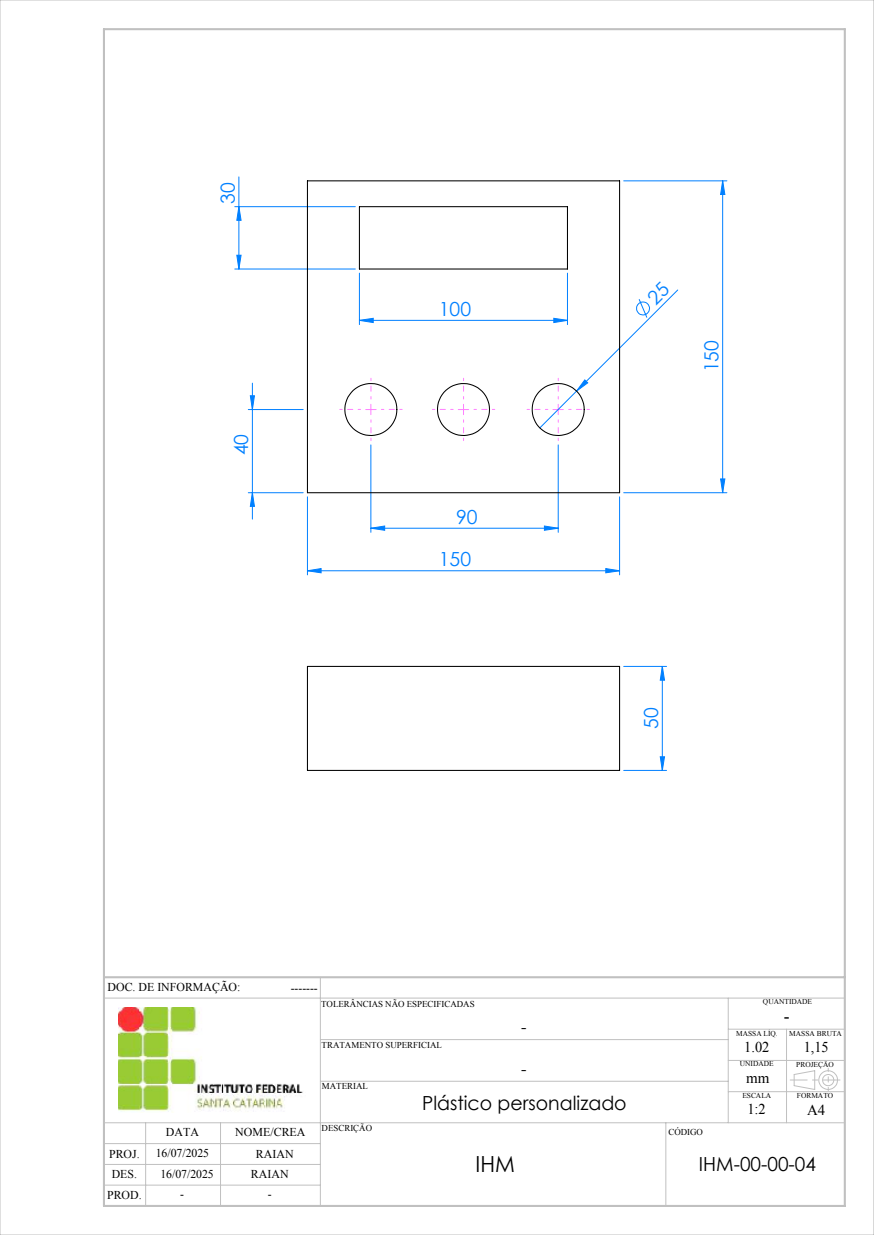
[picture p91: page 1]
IHM; Plástico personalizado; PROJ. DES. PROD.; DATA; NOME/CREA DESCRIÇÃO; CÓDIGO; MATERIAL; TRATAMENTO SUPERFICIAL; ESCALA; FORMATO; UNIDADE; MASSA LÍQ.; QUANTIDADE; RAIAN; IHM-00-00-04 ¹⁶/07/2025; MASSA BRUTA 1,15; PROJEÇÃO

DOC. DE INFORMAÇÃO:

TOLERÂNCIAS NÃO ESPECIFICADAS

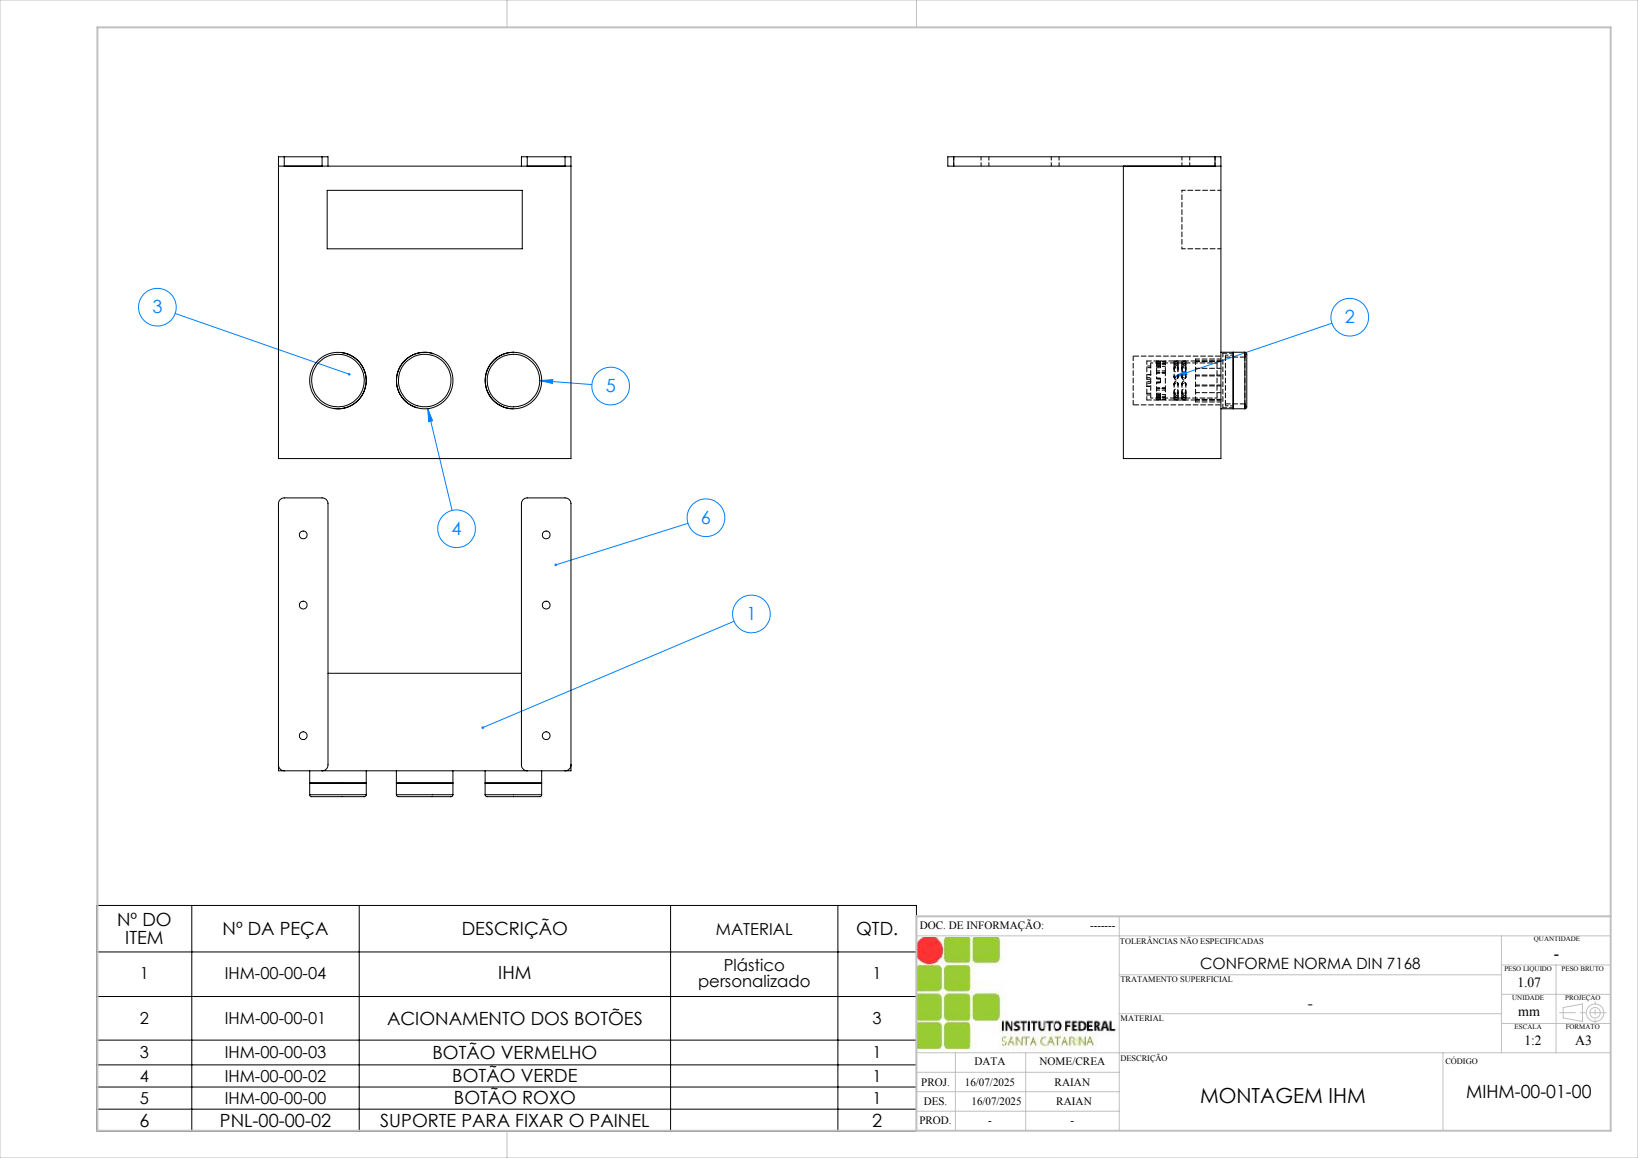
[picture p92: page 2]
MONTAGEM IHM; MIHM-00-01-00 PROJ.; DES. PROD.; DATA; NOME/CREA DESCRIÇÃO; CÓDIGO; MATERIAL; TRATAMENTO SUPERFICIAL; ESCALA; FORMATO; UNIDADE; PROJEÇÃO; QUANTIDADE; DOC. DE INFORMAÇÃO:; RAIAN; CONFORME NORMA DIN 7168

Nº DO ITEM | Nº DA PEÇA | DESCRIÇÃO | MATERIAL | QTD.

TOLERÂNCIAS NÃO ESPECIFICADAS

1 | IHM-00-00-04 | IHM | Plástico personalizado | 1

PESO LIQUIDO PESO BRUTO

2 | IHM-00-00-01 | ACIONAMENTO DOS BOTÕES | | 3
3 | IHM-00-00-03 | BOTÃO VERMELHO | | 1
4 | IHM-00-00-02 | BOTÃO VERDE | | 1
5 | IHM-00-00-00 | BOTÃO ROXO | | 1
6 | PNL-00-00-02 | SUPORTE PARA FIXAR O PAINEL | | 2

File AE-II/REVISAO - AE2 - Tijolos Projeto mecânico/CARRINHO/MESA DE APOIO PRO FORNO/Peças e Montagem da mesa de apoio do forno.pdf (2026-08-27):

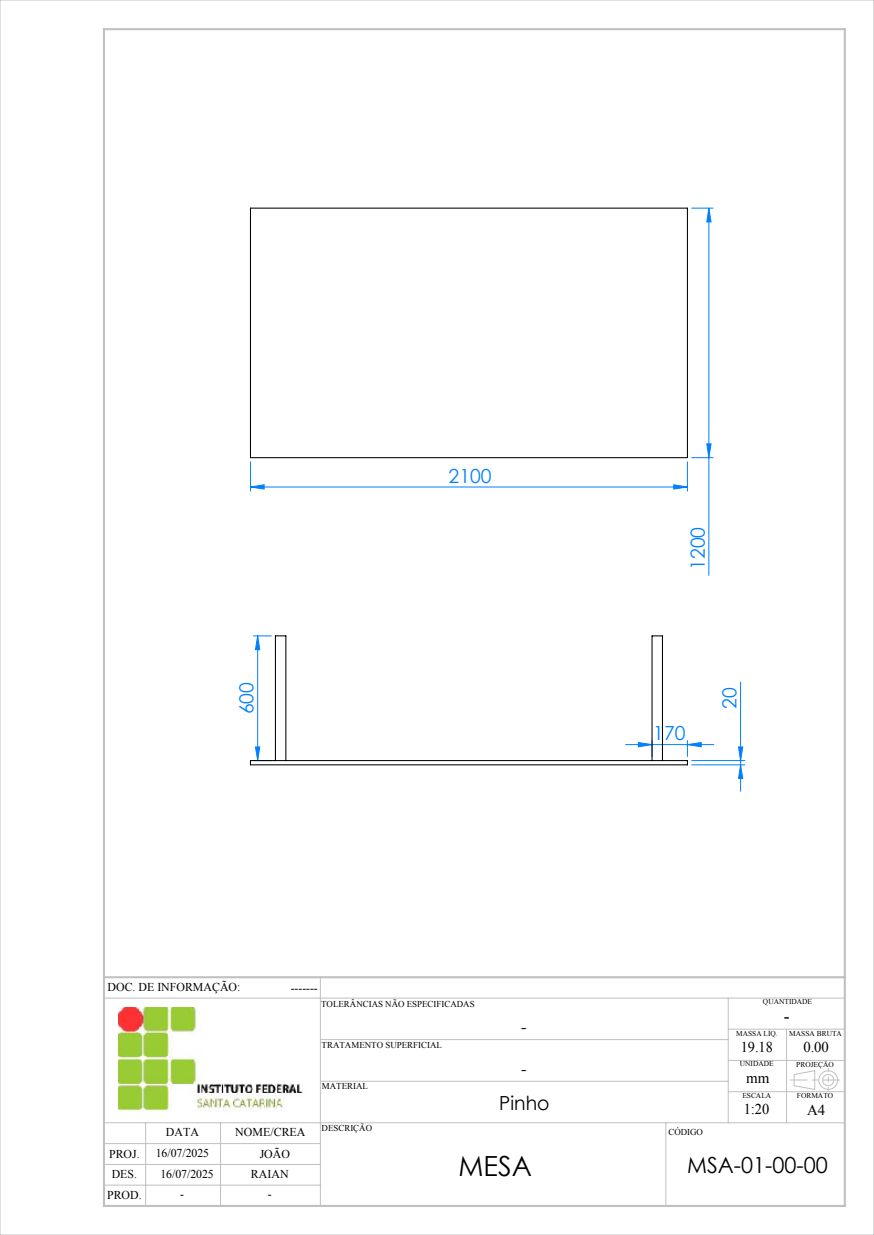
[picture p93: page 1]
MESA; Pinho; PROJ. DES. PROD.; DATA; NOME/CREA DESCRIÇÃO; CÓDIGO; MATERIAL; TRATAMENTO SUPERFICIAL; ESCALA; FORMATO; UNIDADE; MASSA LÍQ.; QUANTIDADE; JOÃO; MSA-01-00-00 ¹⁶/07/2025; MASSA BRUTA 0.00; PROJEÇÃO; RAIAN

DOC. DE INFORMAÇÃO:

TOLERÂNCIAS NÃO ESPECIFICADAS

70

1

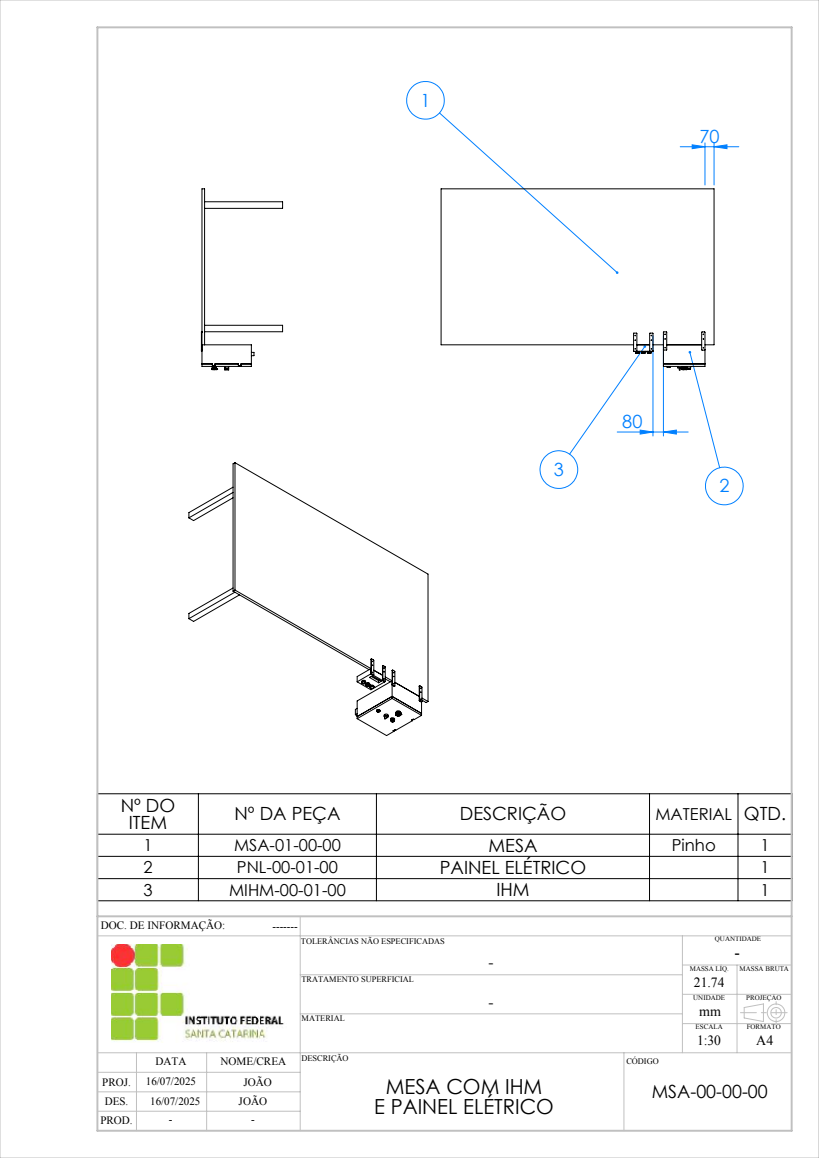
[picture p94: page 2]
PROJ. DES. PROD.; DATA; NOME/CREA DESCRIÇÃO; CÓDIGO; MATERIAL; TRATAMENTO SUPERFICIAL; ESCALA; FORMATO; UNIDADE; MASSA LÍQ.; QUANTIDADE; JOÃO; MSA-00-00-00 ¹⁶/07/2025; MASSA BRUTA; PROJEÇÃO

Nº DO ITEM | Nº DA PEÇA | DESCRIÇÃO | MATERIAL | QTD.
1 | MSA-01-00-00 | MESA | Pinho | 1
2 | PNL-00-01-00 | PAINEL ELÉTRICO | | 1
3 | MIHM-00-01-00 | IHM | | 1

DOC. DE INFORMAÇÃO:

TOLERÂNCIAS NÃO ESPECIFICADAS

MESA COM IHM
E PAINEL ELÉTRICO

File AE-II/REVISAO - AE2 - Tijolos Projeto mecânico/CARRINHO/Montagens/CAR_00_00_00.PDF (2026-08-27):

LÍQUIDA QDT.; CARRINHO; CAR_00_00_00 PROJ.; DATA; NOME/CREA DESCRIÇÃO; CÓDIGO; TRATAMENTO SUPERFICIAL; DOC. DE INFORMAÇÃO:; CONFORME NORMA DIN 7168

6 | ISO - Rack-spur -rectangular 3M 20PA 12FW 10PH 250L---SAll | COMP. REFERENTE CAR_00_01_07. CREMALHEIRA ISO MÓDULO 3, ANGULO DE PRESSÃO 20 , LARGURA 12, ALTURA DA BASE ATE O CENTRO DO DENTE 10, COMPRIMENTO 250. | | | 2

5 | Hexagon Nut ISO -4034 - M8 -N | PORCA SEXTAVADA NORMA ISO 4034 - M8 | | | 2

TOLERÂNCIAS NÃO ESPECIFICADAS

PESO LIQUIDO PESO BRUTO

4 | ISO 10669-8.8-L | ARRUELA ISO 10669-8.8-L | | | 8
3 | CAR_01_00 _02 | CHAPA EXTENSÂO PRANCHA | Chapa F.F 1020 - 2 mm | 0.04 | 2
2 | CAR_00_01 _00 | MONTAGEM EIXO | | 24.69 | 2
1 | CAR_01_00 _01 | PRANCHA CARRINHO | Chapa F.F 1020 - 2 mm | 1.02 | 1

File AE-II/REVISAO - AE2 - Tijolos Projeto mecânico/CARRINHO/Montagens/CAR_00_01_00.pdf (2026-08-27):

MONTAGEM EIXO; CAR_00_01_00 PROJ.; DATA; NOME/CREA DESCRIÇÃO; CÓDIGO; TRATAMENTO SUPERFICIAL; DOC. DE INFORMAÇÃO:; CONFORME NORMA DIN 7168

9 | Hexagon Nut ISO -4032 - M4 -W - N | PORCA SEXTAVADA NORMA ISO 4034 - M8 | | | 4

8 | ISO 4017 -M4 x 35-N | PARAFUSO SEXTAVADO NORMA ISO 4017 M4 | | | 4
7 | ISO 4018 -M8 x 30-WN | PARAFUSO SEXTAVADO NORMA ISO 4018 M8 | | | 1
6 | DIN 94-2x25-C-St | CUPILHA NORMA DIN 94 25 mm | | | 2
5 | CAR_01_01 _01 | RODA CARRNHO | Barra Redonda SAE 1020 - 2" | 0.19 | 2
4 | CAR_01_01 _02 | EIXO CARRINHO | Barra Redonda Tref. SAE 1020 - 5/8" | 24.23 | 1
3 | CAR_01_01 _06 | FUNDO MANCAL DO CARRO | Chapa F.F 1020 - 2 mm | 0.04 | 1
2 | CAR_01_01 _04 | LATERAL MANCAL | Chapa F.F 1020 - 1,5 mm | 0.01 | 2
1 | CAR_01_01 _05 | TOPO DO MANCAL | Chapa F.F 1020 - 2 mm | 0.04 | 1
Nº DO ITEM | Nº DA PEÇA | DESCRIÇÃO | MATERIAL | MASSA LÍQUIDA QDT.

TOLERÂNCIAS NÃO ESPECIFICADAS

PESO LIQUIDO PESO BRUTO

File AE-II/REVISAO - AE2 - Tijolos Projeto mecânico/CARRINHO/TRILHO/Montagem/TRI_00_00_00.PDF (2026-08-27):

TRILHO PROJ.; DATA; NOME/CREA DESCRIÇÃO; CÓDIGO; TRATAMENTO SUPERFICIAL; MASSA LÍQ.; TRI_00_00_00 09/07/2025; MASSA BRUTA

2 | TRI_01_00_00 TRILHO INTERNO | | Material <não especificado> | 0.47 | 1
1 | TRI_01_00_01 TRILHO EXTERNO | | Material <não especificado> | 0.53 | 1
Nº DO ITEM | Nº DA PEÇA | DESCRIÇÃO | MATERIAL | MASSA LÍQUIDA QDT.

DOC. DE INFORMAÇÃO:

TOLERÂNCIAS NÃO ESPECIFICADAS

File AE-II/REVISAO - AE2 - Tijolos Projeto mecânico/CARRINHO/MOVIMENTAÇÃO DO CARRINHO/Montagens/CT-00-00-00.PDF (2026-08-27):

Nº DA PEÇA; DESCRIÇÃO; MATERIAL; MASSA; LÍQUIDA QDT.; MOVIMENTAÇÂO DO CARRINHO; CT-00-00-00 PROJ.; DATA; NOME/CREA DESCRIÇÃO; CÓDIGO; TRATAMENTO SUPERFICIAL; DOC. DE INFORMAÇÃO:; CONFORME NORMA DIN 7168

9 | ESP_00_00_03 | ESPAÇADOR DE EIXO 2 | | 1.39 | 1
8 | ENG-00-01-03 | COROA CORRENTE | Barra Redonda SAE 1020 - 2" | 0.15 | 1
7 | ENG-00-01-02 | COROA | Barra Redonda SAE 1020 - 2" | 0.25 | 1
6 | DIN - Spur gear 3M 20T 20PA 12FW ---S20A75H50L8N | DIN - Spur gear 3M | | | 1

TOLERÂNCIAS NÃO ESPECIFICADAS

PESO LIQUIDO PESO BRUTO

5 | Chain wheel DIN 8192 - A 15Z 08B-1 --15SA8N | Chain Wheel DIN | | | 1

4 | ESP_00_00_01 | ESPAÇADOR DE EIXO 1 | | 1.39 | 2
3 | ETI-00-00-05 | EIXO RODA DENTADA | Barra Redonda SAE 1020 - 1/2" | 0.25 | 1
2 | CT-00-00-02 | BLOCO DE ENGRENAGENS ESQUERDO | | 6.21 | 1
1 | CT-00-00-01 | BLOCO DE ENGRENAGENS DIREITO | | 6.21 | 1

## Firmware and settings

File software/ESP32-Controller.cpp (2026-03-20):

#include <stdio.h>
#include "freertos/FreeRTOS.h"
#include "freertos/task.h"
#include "driver/gpio.h"
#include "driver/adc.h"
#include "esp_log.h"
#include "driver/dac.h"
#include "driver/ledc.h"

static const char *TAG = "ESP32_IO";

// === PINOS ===

#define R1_IN1_GPIO          (gpio_num_t)36   // ADC1_CH6  (R1-IN1)
#define R1_IN2_GPIO          (gpio_num_t)39   // ADC1_CH7  (R1-IN2)

#define DAC_2 (gpio_num_t)25
#define DAC_2 (gpio_num_t)26 

#define SPI_CLK (gpio_num_t)14
#define SPI_MISO (gpio_num_t)12
#define SPI_MOSI (gpio_num_t)13

#define GND (gpio_num_t)14 
#define CINCOV (gpio_num_t)15

#define SCL (gpio_num_t)22
#define SDA (gpio_num_t)21

#define MOTOR1_SAIDA1_GPIO   (gpio_num_t)19   // MOTOR1-SAIDA1
#define MOTOR1_SAIDA2_GPIO   (gpio_num_t)18   // MOTOR1-SAIDA2
#define RESISTENCIA_SAIDA_GPIO (gpio_num_t)5 // RESISTENCIA-SAIDA3

#define UART_TX (gpio_num_t)24 
#define UART_RX (gpio_num_t)25

#define MOTOR2_SAIDA1_GPIO   (gpio_num_t)2   // MOTOR2-SAIDA1
#define MOTOR2_SAIDA2_GPIO   (gpio_num_t)15   // MOTOR2-SAIDA2

#define GND (gpio_num_t)29
#define CINCOVSAIDA (gpio_num_t)30

void setup(){
    ESP_LOGI(TAG, "=== ESP32 ESP-IDF + FreeRTOS iniciado (baseado na imagem) ===");

    // ================== CONFIGURAÇÃO DAS SAÍDAS DIGITAIS ==================
    gpio_set_direction(MOTOR1_SAIDA1_GPIO,   GPIO_MODE_OUTPUT);
    gpio_set_direction(MOTOR1_SAIDA2_GPIO,   GPIO_MODE_OUTPUT);
    gpio_set_direction(RESISTENCIA_SAIDA_GPIO, GPIO_MODE_OUTPUT);
    gpio_set_direction(MOTOR2_SAIDA1_GPIO,   GPIO_MODE_OUTPUT);
    gpio_set_direction(MOTOR2_SAIDA2_GPIO,   GPIO_MODE_OUTPUT);

    // Estado inicial seguro (tudo desligado)
    gpio_set_level(MOTOR1_SAIDA1_GPIO,   0);
    gpio_set_level(MOTOR1_SAIDA2_GPIO,   0);
    gpio_set_level(RESISTENCIA_SAIDA_GPIO, 0);
    gpio_set_level(MOTOR2_SAIDA1_GPIO,   0);
    gpio_set_level(MOTOR2_SAIDA2_GPIO,   0);

    // ================== CONFIGURAÇÃO ADC 12 BITS (datasheet seção 4.2) ==================
    adc1_config_width(ADC_WIDTH_BIT_12);                    // Resolução 12 bits (0-4095)
    adc1_config_channel_atten(ADC1_CHANNEL_6, ADC_ATTEN_DB_11); // GPIO34 – faixa ~0-3,3V
    adc1_config_channel_atten(ADC1_CHANNEL_7, ADC_ATTEN_DB_11); // GPIO35 – faixa ~0-3,3V

}
//Testes Digitais
static const struct {
    gpio_num_t pin;
    const char* nome;
} saidas[] = {
    {SPI_CLK,       "SPI_CLK"},
    {SCL,           "SCL"},
    {SDA,           "SDA"},
    {MOTOR1_SAIDA1_GPIO, "M1 A1"},
    {MOTOR1_SAIDA2_GPIO, "M1 A2"},
    {RESISTENCIA_SAIDA_GPIO, "Resist."},
    {UART_TX,       "UART_TX"},
    {UART_RX,       "UART_RX"},
    {MOTOR2_SAIDA1_GPIO, "M2 A1"},
    {MOTOR2_SAIDA2_GPIO, "M2 A2"},
    {SPI_MISO,      "SPI_MISO"},
    {SPI_MOSI,      "SPI_MOSI"},
};

void TesteDigitais(void)
{
    esp_err_t err = ESP_OK;

    while (err == ESP_OK)
    {
        for (size_t i = 0; i < sizeof(saidas)/sizeof(saidas[0]) && err == ESP_OK; i++)
        {
            err = gpio_set_level(saidas[i].pin, 1);
            if (err == ESP_OK) vTaskDelay(pdMS_TO_TICKS(100));

            if (err == ESP_OK) {
                err = gpio_set_level(saidas[i].pin, 0);
                if (err == ESP_OK) vTaskDelay(pdMS_TO_TICKS(100));
            }
        }

        if (err == ESP_OK) {
            vTaskDelay(pdMS_TO_TICKS(1000));  // pausa entre ciclos
        }
    }

    if (err != ESP_OK) {
        ESP_LOGE(TAG, "Erro detectado no teste digital");
    }
}
// ESTE DAC (RAMPA 0 → 255 em exatamente 2 segundos) 

void TestePWM(void)
{
    ESP_LOGI("TESTE_PWM", "Iniciando teste PWM rampa duty (pino %d)", MOTOR1_SAIDA1_GPIO);

    // Configuração do timer PWM
    ledc_timer_config_t timer_config = {
        .speed_mode       = LEDC_LOW_SPEED_MODE,
        .duty_resolution  = LEDC_TIMER_10_BIT,
        .timer_num        = LEDC_TIMER_0,
        .freq_hz          = 5000,
        .clk_cfg          = LEDC_AUTO_CLK
    };
    ESP_ERROR_CHECK(ledc_timer_config(&timer_config));

    // Canal PWM – ordem correta dos campos (igual ao header ledc.h)
    ledc_channel_config_t channel_config = {
        .gpio_num       = MOTOR1_SAIDA1_GPIO,
        .speed_mode     = LEDC_LOW_SPEED_MODE,
        .channel        = LEDC_CHANNEL_0,
        .intr_type      = LEDC_INTR_DISABLE,
        .timer_sel      = LEDC_TIMER_0,
        .duty           = 0,
        .hpoint         = 0
    };
    ESP_ERROR_CHECK(ledc_channel_config(&channel_config));

    // Rampa de duty 0 → 1023 em ~2 segundos
    const int passos = 1024;
    const int delay_por_passo = 2000 / passos;  // ≈ 1.95 ms por passo

    for (int duty = 0; duty <= 1023; duty++) {
        ledc_set_duty(LEDC_LOW_SPEED_MODE, LEDC_CHANNEL_0, duty);
        ledc_update_duty(LEDC_LOW_SPEED_MODE, LEDC_CHANNEL_0);
        vTaskDelay(pdMS_TO_TICKS(delay_por_passo));
    }

    // Desliga no final
    ledc_set_duty(LEDC_LOW_SPEED_MODE, LEDC_CHANNEL_0, 0);
    ledc_update_duty(LEDC_LOW_SPEED_MODE, LEDC_CHANNEL_0);

    ESP_LOGI("TESTE_PWM", "Rampa PWM finalizada");
}

void loop(){
    TestePWM();
    TesteDigitais();
}

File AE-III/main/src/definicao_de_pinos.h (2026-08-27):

/*
 * definicao_de_pinos.h
 *
 *  Created on: 13 de abr. de 2026
 *      Author: Gabriel
 */

#ifndef MAIN_SRC_DEFINICAO_DE_PINOS_H_
#define MAIN_SRC_DEFINICAO_DE_PINOS_H_

#include "driver/gpio.h"
#include "hal/gpio_types.h"
#include "soc/gpio_num.h"

#define DEBUG 1

#define PINO_LIGA GPIO_NUM_2
#define PINO_INICIAR GPIO_NUM_14
#define PINO_MOTOR_E GPIO_NUM_4
#define PINO_MOTOR_D GPIO_NUM_16
#define PINO_RESISTENCIA GPIO_NUM_5

void setup_pinos(){
	gpio_set_direction(PINO_LIGA, GPIO_MODE_INPUT);
	gpio_set_direction(PINO_INICIAR, GPIO_MODE_INPUT);
	gpio_set_direction(PINO_MOTOR_D, GPIO_MODE_OUTPUT);
	gpio_set_direction(PINO_MOTOR_E, GPIO_MODE_OUTPUT);
	gpio_set_direction(PINO_RESISTENCIA, GPIO_MODE_OUTPUT);
	
	gpio_set_pull_mode(PINO_LIGA, GPIO_PULLUP_ENABLE);
}

#endif /* MAIN_SRC_DEFINICAO_DE_PINOS_H_ */

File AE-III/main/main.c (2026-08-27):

#include <stdint.h>
#include <stdio.h>
#include <stdbool.h>
#include <sys/unistd.h>
#include <unistd.h>
#include <driver/gpio.h>
//#include "soc/clk_tree_defs.h"
#include "src/adc.h"
#include "src/controle.h"
//#include "src/controle_portas.h"
#include "src/definicao_de_pinos.h"
#include "src/controle_portas.c"
#include "src/temporizador.c"
#include "src/temporizador.h"
#include "src/adc.c"
#include "src/controle.c"

// ================================================
//  MÁQUINA DE ESTADOS - Forno 
// ================================================


enum Estado {
	DESLIGADO,
	AGUARDANDO_SET_POINT,
	INICIO_DE_PROCESSO,
	CARREGAMENTO,
	FORNO_CARREGADO,
	COZIMENTO,
	FIM_DE_PROCESSO,
	DESCARREGAMENTO,
	FECHAMENTO_DE_PORTAS
};


uint8_t estadoAtual = DESLIGADO;
uint8_t estadoAnterior = 0;
bool a = false;

void app_main(){
	gptimer_handle_t timer_tempo = NULL;
	
	adc_oneshot_unit_handle_t adc;
	
	setup_temporizador(&timer_tempo);
	
	gptimer_start(timer_tempo);
	
	setup_pinos();
	setup_ADC(&adc);

	
	
	uint8_t aux = 0;
	bool liga = 0;
	
	double kp = 0.01654;
	double kd = 0;
	double ti = 6954.1029;
	double T= 1.0;
	double ref = 600.0;
	
	double  u = 0;
	double u_anterior = 0;
	double  e = 0;
	double e_anterior = 0;
	double e_2_anterior = 0;
	
	double alpha = kp*(1.0 + (T/(2.0*ti)));
	double beta = kp * ((T/(2.0*ti))-1.0);
	//float omega = kp * (kd/T);
	
	while(true){
		
		
		
		if(gpio_get_level(PINO_LIGA)){
			liga = 1;
		 	printf("Forno LIGADO");
	 	}
		
		if(aux != segundos){
			//printf("ciclo: %d\n", (uint16_t)ciclo_atual);
			e = ref - printa_ADC(&adc, CANAL_TERMOPAR, -60, u_anterior);;
			u = u_anterior + (alpha * e) + (beta * e_anterior);
			
			
			
			//printf("u: %f u-1: %f e: %f e-1: %f e-2:%f alpha: %f beta: %f\n", u, u_anterior, e, e_anterior, e_2_anterior, alpha, beta);
			
			u_anterior = u;
			e_2_anterior = e_anterior;
			e_anterior = e;
			
			if(u > 1.0){
				u =1.0;
			}
			
			if(u < 0.1){
				u = 0.0;
			}
			
		}
		aux = segundos;
		
		if(liga){
			PWM_resistencia(10000, u);
		}
		
		/*switch (estadoAtual) {
	
		    case DESLIGADO:
		    	// Máquina Desligada
			    // Condições de saída:
			    // - Botão Ligar pressionado
				printf("%d",gpio_get_level(PINO_LIGA) );
			    if (gpio_get_level(PINO_LIGA) == 1) {
			    	estadoAtual = AGUARDANDO_SET_POINT;
			    }
		    break;
		
		    case AGUARDANDO_SET_POINT:
			    int setpoint_temperatura = 0;
				scanf("digite a temperatura desejada: %d", &setpoint_temperatura);
			    if (setpoint_temperatura >= 0){
			    // Estado 3 - Máquina Ligada
			    	estadoAtual = INICIO_DE_PROCESSO;
			    }
		    break;
		
		    case INICIO_DE_PROCESSO:
				//abre a porta e retorna 1 quando termina
			    if (move_porta(ABRE, &adc)) {
			    	estadoAtual = CARREGAMENTO;
			    }
			break;
		
		    case CARREGAMENTO:
			    //liga motores do carrinho
			   	if (true) {
			    	estadoAtual = FORNO_CARREGADO;
			    }
		    break;
		
		    case FORNO_CARREGADO:
			    // Forno Carregado
			    if (move_porta(FECHA,&adc)) {
			    	estadoAtual = COZIMENTO;
			    }
			break;
		
		    case COZIMENTO:
			    // Liga a Temperatura e Processo de cozimento
			    // Ações: Ligar controle de temperatura + geração de gráficos
				uint16_t leitura = 0;
				
				if(aux != segundos){
					leitura = printa_ADC(&adc, CANAL_TERMOPAR);
				}
				aux = segundos;
				
			    if (leitura > 500) {
			    	estadoAtual = FIM_DE_PROCESSO;
			    }
		    break;
		
		    case FIM_DE_PROCESSO:
			    // Descarregamento
			    // Ações: Desligar resistências, parar gráficos, abrir portas
			    if (move_porta(ABRE,&adc)) {
			    	estadoAtual = DESCARREGAMENTO;
			    }
		    break;
		
		    case DESCARREGAMENTO:
			    // Ações: Aciona carro de saída
				if (true) {
			    	estadoAtual = FECHAMENTO_DE_PORTAS;
			    }
		    break;
		
			case FECHAMENTO_DE_PORTAS:
			    // Fechamento de porta
			    // Ações: Fechar a porta
			    if (move_porta(FECHA,&adc)) {
			        // Volta para o início ou estado de espera
			    	estadoAtual = AGUARDANDO_SET_POINT;   // ou ESTADO_2_AGUARDANDO_SET_POINT
			    }
			break;
		}

		//printa estado atual
		if(estadoAtual != estadoAnterior){
			printf("estado atual:");
			switch (estadoAtual) {
				
				case DESLIGADO:
					printf("DESLIGADO\n");
				break;
				
				case AGUARDANDO_SET_POINT:
					printf("AGUARDANDO_SET_POINT\n");
				break;
				
				case INICIO_DE_PROCESSO:
					printf("INICIO_DE_PROCESSO\n");
				break;
				
				case CARREGAMENTO:
					printf("CARREGAMENTO\n");
				break;
				
				case FORNO_CARREGADO:
					printf("FORNO_CARREGADO\n");
				break;
				
				case COZIMENTO:
					printf("COZIMENTO\n");
				break;
				
				case FIM_DE_PROCESSO:
					printf("FIM_DE_PROCESSO\n");
				break;
				
				case DESCARREGAMENTO:
					printf("DESCARREGAMENTO\n");
				break;
				
				case FECHAMENTO_DE_PORTAS:
					printf("FECHAMENTO_DE_PORTAS\n");
				break;
			}
		}
		estadoAnterior = estadoAtual;*/
		
		usleep(10000);
	}
}

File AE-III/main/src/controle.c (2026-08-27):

/*
 * controle.c
 *
 *  Created on: 17 de abr. de 2026
 *      Author: Raian
 */

#include "controle.h"
#include "driver/gpio.h"
#include "temporizador.h"
#include "definicao_de_pinos.h"
#include <stdint.h>

void PWM_resistencia(uint16_t periodo_m, float duty) {
    // Calcula o tempo total em ms desde o início
    uint32_t tempo_total_ms = ((uint32_t)horas * 3600 * 1000) + ((uint32_t)minutos * 60 * 1000) + ((uint32_t)segundos * 1000) + milisegundos;
    
    // Calcula a fase dentro do ciclo atual (0 a periodo_m - 1)
    uint16_t fase = tempo_total_ms % periodo_m;
    
    // Calcula o tempo "on" baseado no duty cycle (em ms)
    uint16_t tempo_on = (periodo_m * duty);
    
    // Aciona o pino: alto se dentro do tempo "on", baixo caso contrário
    if (fase < tempo_on) {
        gpio_set_level(PINO_RESISTENCIA, 1);
    } else {
        gpio_set_level(PINO_RESISTENCIA, 0);
    }
    
    // Opcional: atualiza ciclo_atual para debug (progresso em % do ciclo)
    ciclo_atual = (fase * 100) / periodo_m;
}

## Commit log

2025-08-20 [add] Added circuit control simulation file
2025-11-02 [feature] Added new furnace power simulation files
